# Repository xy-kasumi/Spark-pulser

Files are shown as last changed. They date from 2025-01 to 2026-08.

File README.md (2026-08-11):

# Pulser Board

🚧 Under Construction 🚧

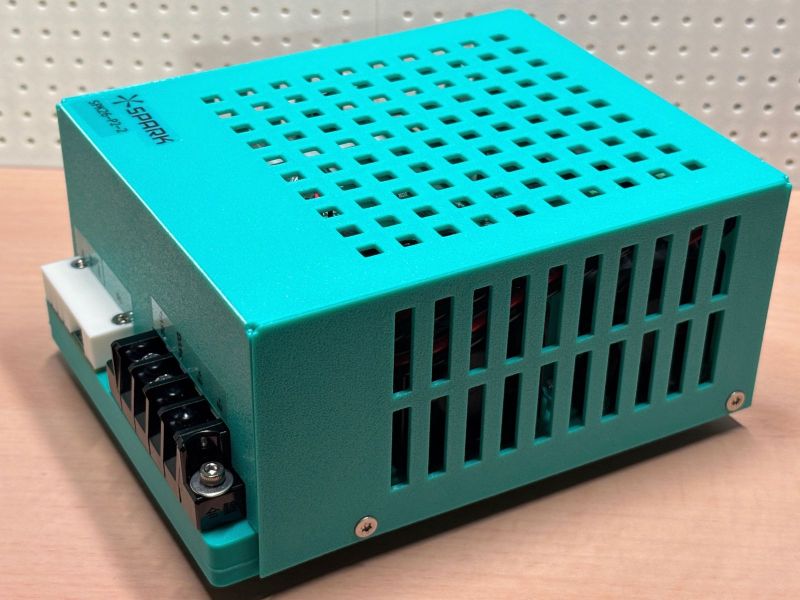
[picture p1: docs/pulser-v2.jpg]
Pulser V2


Open-source EDM module.

Explicitly designed for plunge EDM.
But probably will work for wire EDM too.

Created for https://github.com/xy-kasumi/Spark project.

## Capability (V2)

* 10A max pulse (see [module spec](./docs/pulser.md) for details)
* Designed for reliablity and modular testability (especially stress testing)

Assembly
* PCB (`pcb/` JLCPCB friendly KiCad files (all manufacturable using "Economical PCBA" process))
  * ctrl-r2
  * hv-r4
  * hc-r3
* firmware (ATtiny1616), for `ctrl` and `hv`
* enclosure: 3D print data in `assy`
* needs a few other parts (12V fans & heatsinks)

# Legacy

There was V1 (repo `PULSER-*` tags).
It was "feature-complete", but lacked reliability & testability.

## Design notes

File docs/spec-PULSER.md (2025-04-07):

# PULSER r2 PCB Spec / Cheatsheet for Firmware Developer

This document specifies the PCB hardware interface needed for firmware development,
to meet the requirements defined in [user-PULSER.md](user-PULSER.md).

## Conditions to consider

* Host is not working
  * Control connector is disconnected
  * Host turned off, blank firmware, initializing
* Thermistor wire is broken

Firmware must map these state to well-defined safe behavior.

## uC Overview

uC is Raspberry Pi Pico 2 board.
* [Pico 2 board datasheet](https://datasheets.raspberrypi.com/pico/pico-2-datasheet.pdf)
* [RP2350 chip datasheet](https://datasheets.raspberrypi.com/rp2350/rp2350-datasheet.pdf)

uC operating environment
* 5V 1A powered, regulated down from 12V power
* System clock: 150 MHz
* Firmware write via 3-pin QI connector SWD interface

## uC Connections

| Pin  | Pin Feature  | Connected to | Note |
|---|---|---|---|
| GP0  | I2C0 SDA | I2C_SDA | to host; pulled up to 3.3V by 10kΩ on PCB |
| GP1  | I2C0 SCL | I2C_SCL | to host; pulled up to 3.3V by 10kΩ on PCB |
| GP2  | GPIO (IN) | GATE | to host; direct |
| GP3  | - | - | - |
| GP4  | GPIO (OUT) | LED_STATUS | white LED, digital H = ON |
| GP5  | - | - | - |
| GP6  | - | - | - |
| GP7  | GPIO (OUT) | MUX_V0 | Controls bridge driver V0 (IN) |
| GP8  | - | - | - |
| GP9  | GPIO (OUT) | MUX_VC | Controls bridge driver Vcom (IN) |
| GP10 | - | - | - |
| GP11 | - | - | - |
| GP12 | - | N/C | - |
| GP13 | - | N/C | - |
| GP14 | I2C1 SDA | TS_I2C_SDA | Temp sensor chip I2C |
| GP15 | I2C1 SCL | TS_I2C_SCL | Temp sensor chip I2C |
| GP16 | - | N/C | - |
| GP17 | GPIO (OUT) | GATE_IG | Controls bridge driver for ignition voltage. |
| GP18 | PWM1A (OUT)  | GATE_MAIN_PWM  | Controls buck converter gate |
| GP19 | - | N/C | - |
| GP20 | - | N/C | - |
| GP21 | - | N/C | - |
| GP22 | - | N/C | - |
| GP26 | ADC0 | CURR_DETECT | Current sense chip |
| GP27 | - | N/C | - |
| GP28 | - | N/C | - |

* N/C: No Connection

### Gate input filter
Since correctness of GATE is critical and it's used in noisy environment,
it should employ noise-filtering. (i.e. only detect change if the value persists for more than 1us).

### Pulse generation (GATE_IG, GATE_MAIN_PWM, CURR_DETECT)

Normal operation sequence:
* 0. setup mux
* 1. enable GATE_IG, wait for ignition by monitoring CURR_DETECT
* 2. in parallel:
 * 2.a shutdown GATE_IG after some fixed time (e.g. 10us)
 * 2.b start buck converter, control PWM frequency by monitoring CURR_DETECT

If the ignition time is too short, consider it as short-circuit and don't start buck converter.
Slow GATE_IG shutdown doesn't break anything; rather it just increases time to recover 100V voltage.
Fast GATE_IG means less 100V capacity wasted, but risks premature shutdown of discharge.

Buck converter
* PWM frequency: 500kHz (2us)
* Maximum rate of current change: 36V / 10uH (L4) = 3.6A/us
  * 1% duty: +0.18A/cycle

As there is current sensing delay, PWM duty should start small and change speed should be limited.

#### Current detection

CURR_DETECT is analog output of hole current sensor chip.
ADC Vref is connected to 3.0V reference voltage.
CURR_DETECT is capped by diode to not exceed 3.0V.

* ACS724LLCTR-30AU
* [datasheet](https://www.allegromicro.com/-/media/files/datasheets/acs724-datasheet.ashx)
* "30AU": 0~30A, 133mV/A
* Vout(I=0) = Vcc x 0.1 = 0.5V
* Filter fc=180kHz

Should sample at highest possible ADC resolution to improve current control.

ADC should set PS(GPIO23)=1 to reduce Pico 2 on-board voltage supply ripple.

### Output mux (MUX_*)
Output stage consists of 3 half-bridges.
This enables polarity change & choosing output (work vs grind).

MOSFET driver
* UCC27288
* [datasheet](https://www.ti.com/lit/ds/symlink/ucc27288.pdf)

MOSFETs (both are N-ch)
* BSC110N15NS5
* [datasheet](https://www.infineon.com/dgdl/Infineon-BSC110N15NS5-DataSheet-v02_06-EN.pdf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)

* V0 = WORK
* V1 = GRIND
* VC = TOOL

Allowed configuration:

Keep driver active config
| POLARITY | V0 | VC |
|---|----|----|
| TPWN, TPGN | L  | H  |
| OFF, TNWP, TNGP  | H  | L  |
| Trans | Z  | Z  |

* L: only enable L
* H: only enable H
* Z: disable both

Any any moment, configurations other than this is disallowed.

OFF is L instead of Z, to properly boot-strap gate driver capacitors.

As mux doesn't need fast switching, transition period should be long (more than 500ns)
to avoid any possibility of shoot-through.

Keep driver active config
* pros: easier to ensure gate driver bootstrap
* cons: might cause uncessary electrolysis

Turn-off unused config
* pros: minimize electrolysis, slightly reduce safety risk
* cons: probably need periodic activation to keep driver boostrapped

### Temperature sensor

TMP102 chip
* [datasheet](https://www.ti.com/lit/ds/symlink/tmp102.pdf)
* I2C connection
* ADD0: V+ (see eratta)
* device address: 1001001 (0x49)

The chip is mounted close to hottest MOSFETs.
We need to determine upper bound of operating condition, and reject to run discharges if exceeded.

Registers are 16bit.
Reg 0x00: temperature (12bit, left-padded, big endian.)

Top 8 bit is signed 8 bit int, temperature in °C.

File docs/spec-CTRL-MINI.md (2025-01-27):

# CTRL-MINI-ED (r0) PCB Spec / Cheatsheet for Firmware Developer

This document specifies the PCB hardware interface needed for firmware development,
to meet the requirements defined in [user-README-CTRL-MINI.md](user-README-CTRL-MINI.md).

## Conditions to consider

* MD boards are (partially) unavailable
* ED board is unavailable

Firmware must map these states to well-defined safe behaviors.

## uC Overview

The uC is a Raspberry Pi Pico 2 board.
* [Pico 2 board datasheet](https://datasheets.raspberrypi.com/pico/pico-2-datasheet.pdf)
* [RP2350 chip datasheet](https://datasheets.raspberrypi.com/rp2350/rp2350-datasheet.pdf)

uC operating environment
* 5V 1A powered, regulated down from 12V main power
* System clock: 150 MHz
* Firmware write via 3-pin QI connector SWD interface

## uC Connections

| Pin  | Pin Feature | Connected to | Note |
|---|---|---|---|
| GP0  | UART0 TX | MUI-RX | RasPi probe (serial) |
| GP1  | UART0 RX | MUI-TX | RasPi probe (serial) |
| GP2  | SPI0 SCK | MD (all) | |
| GP3  | SPI0 SDI | MD (all) | |
| GP4  | SPI0 SDO | MD (all) | |
| GP5  | - | ED Conn Pin 3 | N/C (r1), MODE (r0) |
| GP6  | I2C1 SDA | ED Conn Pin 4 | I2C SDA (r1), SENSE_GATE (r0) |
| GP7  | I2C1 SCL | ED Conn Pin 6 | I2C SCL (r1), DCHG_TARG_PWM (r0) |
| GP8  | GPIO (OUT) | ED Conn Pin 7 | GATE (r1), DCHG_GATE (r0) |
| GP9  | GPIO (IN) | ED Conn Pin 8 | DETECT (r1), DCHG_DETECT (r0) |
| GP10 | - | N/C | |
| GP11 | - | N/C | |
| GP12 | - | N/C | |
| GP13 | - | N/C | |
| GP14 | - | N/C | |
| GP15 | - | N/C | |
| GP16 | GPIO (OUT) | MD (all) DIR | |
| GP17 | GPIO (OUT) | MD (0) STEP | |
| GP18 | GPIO (OUT) | MD (1) STEP | |
| GP19 | GPIO (OUT) | MD (2) STEP | |
| GP20 | GPIO (OUT) | MD (0) CSN | |
| GP21 | GPIO (OUT) | MD (1) CSN | |
| GP22 | GPIO (OUT) | MD (2) CSN | |
| GP26 | - | ED Conn Pin 5 | N/C (r1), SENSE_CURR (r0) |
| GP27 | - | N/C | |
| GP28 | - | N/C | |

* N/C: No Connection

MD r0, ED r1 is assumed.
ED r0 pin notes are left for historical reference.

## MD boards

The MD board is a 14-pin child board, taking 3.3V logic power and 12V power input.

Each MD board has:
* A single TMC2130 stepper driver motor
* On-PCB configuration jumpers for:
  * Phase current (0.2A vs 0.4A)
  * Power voltage (5V vs 12V)

They're controlled by SPI & "STEP/DIR" interface.
SPI bus connects uC and 3 MD boards.

To address each chip individually, CSN pins are used.
CSNs are GPIO pins, so firmware needs to manually toggle them when doing SPI transactions.

# ED board

Nothing is done in CTRL-MINI. Just a direct connection.
See [user-README-CTRL-MINI-ED.md](user-README-CTRL-MINI-ED.md) for details.

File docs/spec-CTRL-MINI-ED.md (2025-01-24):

# CTRL-MINI-ED PCB Spec / Cheatsheet for Firmware Developer

This document specifies the PCB hardware interface needed for firmware development,
to meet the requirements defined in [user-README-CTRL-MINI-ED.md](user-README-CTRL-MINI-ED.md).

## Conditions to consider

* Host is not working
  * Control connector is disconnected
  * Host turned off, blank firmware, initializing
* Thermistor wire is broken

Firmware must map these state to well-defined safe behavior.

## uC Overview

uC is Raspberry Pi Pico 2 board.
* [Pico 2 board datasheet](https://datasheets.raspberrypi.com/pico/pico-2-datasheet.pdf)
* [RP2350 chip datasheet](https://datasheets.raspberrypi.com/rp2350/rp2350-datasheet.pdf)

uC operating environment
* 5V 1A powered, regulated down from 36V main power
* System clock: 150 MHz
* Firmware write via 3-pin QI connector SWD interface

## uC Connections

|Pin | Pin Feature | Connected to | Note |
|----|---|---|---|
|GP0 | I2C0 SDA | I2C_SDA | to host; pulled up to 3.3V by 10kΩ on PCB |
|GP1 | I2C0 SCL | I2C_SCL | to host; pulled up to 3.3V by 10kΩ on PCB |
|GP2 | GPIO (IN) | GATE | to host; direct |
|GP3 | GPIO (OUT)  | DETECT  | to host; direct |
|GP4 | GPIO (OUT)  | LED_STATUS | white LED, digital H = ON |
|GP5 | GPIO (OUT)  | LED_POWER  | red, digital H = ON |
|GP6 | - | N/C | |
|GP7 | - | N/C | |
|GP8 | GPIO (OUT)  | MUX_POL = POL | Relay gate drive. OFF: COM(TOOL)=-,VO_AUX=+, ON: COM(TOOL)=+, VO_AUX=- |
|GP9 | GPIO (OUT)  | MUX_WG = SEL | Relay gate drive. OFF: V0(WORK)=ON, ON: V1(GRINDER)=ON |
|GP10| GPIO (OUT)  | MUX_EN = EN | Relay gate drive. OFF: cut off driver, ON: connect driver |
|GP11| - | N/C | |
|GP12| - | N/C | |
|GP13| - | N/C | |
|GP14| - | N/C | |
|GP15| - | N/C | |
|GP16| GPIO (IN) | CURR_TRIGGER | 3.3V output from Comparator U5 |
|GP17| - | N/C | |
|GP18| PWM1A (OUT) | CURR_GATE_PWM | analog filter; see below |
|GP19| - | N/C | |
|GP20| PWM2A (OUT) | CURR_THRESH_PWM | analog filter; see below |
|GP21| - | N/C | |
|GP22| - | N/C | |
|GP26| ADC0 | TEMP_HS | Thermistor - resistor voltage divider |
|GP27| - | N/C | |
|GP28| - | N/C | |

* N/C: No Connection

### Pulse generator (CURR_GATE_PWM, CURR_THRESH_PWM, DETECT)
Main MOSFET current flow
```
100V|36V --(E+)-- discharge gap --(E-)-- drain:MOSFET:source --(FB)-- 220mΩ(±5%) --- GND
```

Voltage at FB is used for current feedback control of MOSFET driving, and also for current detection.

| ΔIp or Ip | FB | GATE | Approx |
|---|----|---|---|
| ΔIp = 100mA | ΔFB = 22mV (min: 21mV, max: 23mV) | ΔGATE = 37mV | 1/89 x 3.3V |
| Ip = 1A | FB = 0.22V (min: 0.21V, max: 0.23V) | GATE = 0.37V | 10/89 x 3.3V |
| Ip = 8A | FB = 1.76V (min: 1.67V, max: 1.85V) | GATE = 2.98V | 80/89 x 3.3V |

#### Current / voltage control
```
CURR_GATE_PWM --> gate-filter --(CURR_GATE)--> feedback-controlled MOSFET
CURR_THRESH_PWM --> thresh-filter --> -:voltage comparator
CURR_DETECT <-- voltage comparator:+ <-- FB filter --- FB
```

#### Gate filter
```
CURR_GATE_PWM (3.3V digital) --> 59% volt divider (Z=278Ω) --> 10uH --(pull down via 10nF) --> +:controller opAmp
```

This forms 2nd-order LPF with Fc=500kHz.
Simulation shows that
* 1us rise time for step input
* 2MHz PWM yields ripple of up to 5% of full scale (0.17V; corresponds to 750mA in Ip)
  * 2MHz PWM means 75 cycles (sys clock = 150MHz)
* allows room for current-shaping in the future

To achieve more accurate current control, pre-computed delta-sigma pattern table and PIO should be used.

#### Thresh filter
```
CURR_THRESH_PWM (3.3V digital) --> 10kΩ --(pull down via 10nF) --> -:voltage comparator
```
1st order LPF with Fc=1.6kHz.
1MHz PWM should yield accurate enough analog signal.

#### FB filter
FB signal goes through 2nd order LPF with Fc=1MHz to suppress noise.
This might introduce latency of 1us, but there's nothing uC can do.

### Relays (MUX_EN, MUX_POL, MUX_WG)
```
uC pin --- 1kΩ --(pull down via 47kΩ)-- gate:MOSFET
+12V --- relay coil (+ flywheel diode) -- drain:MOSFET:source --- GND
```

MOSFET gate has ringing-limiting in-line resistor (1k), and pull-down (47k).

Thus, when uC is not iniailized (high-Z GPIO), relay is OFF. uC also doesn't need to pull-down.

MOSFET: Vishay Si2304DDS
* [datasheet](https://www.lcsc.com/datasheet/lcsc_datasheet_2410121816_Vishay-Intertech-SI2304DDS-T1-GE3_C56372.pdf)
* Full-turn on around Vgs~3V

Relay: Omron G2RL-24 DC12
* [datasheet](https://omronfs.omron.com/en_US/ecb/products/pdf/en-g2rl.pdf)
* 2-pole (DPDT; 2c), sealed, 12V coil
* coil current 33mA, 12V
* turn on time: 15ms max
* turn off time: 5ms max
* rated switching load: 8A @ 30VDC (durability: 30K operations)
* rated carry current: 8A @ 70℃
* contact resistance: 100mΩ max

### Temperature sensor (TEMP_HS)
connection: 3.3V --- thermistor --(TEMP_HS)-- 47k --- GND

thermistor: 100kΩ NTC thermistor
* EPCOSB57861S0104F040
* R(T=25℃): 100kΩ±1%
* B-value: 4540K±1%
* [datasheet](https://docs.rs-online.com/838f/0900766b815ec91a.pdf)

This graph/table shows relationship within 5℃ accuracy.

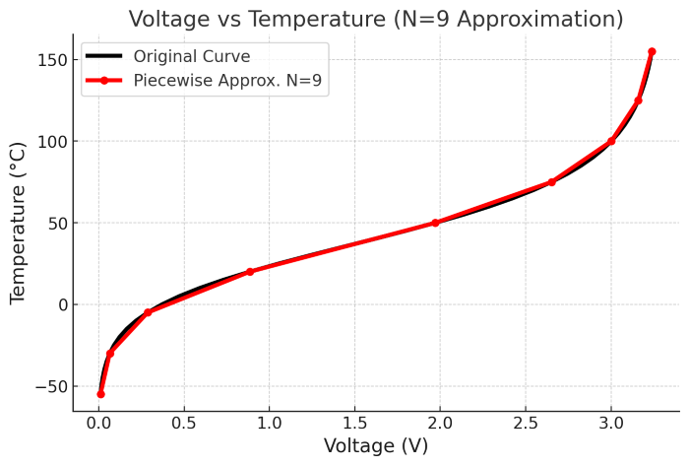
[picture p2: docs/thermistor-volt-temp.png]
thermistor-temp


TEMP_HS(V) | Temp(°C)
-----|-----
0.29 | -5
0.89 | 20
1.97 | 50
2.65 | 75
3.01 | 100
3.16 | 125

Outside this range, firmware should refuse to run (show error) until reset.

Thermistor is inserted to heatsink with silicon heat paste.

Heasink has MOSFET (Q4), resistor (R17), OR-diode (D6).
They're pretty heat resistant. However, it's better to think 60℃ or close as max allowed temp for heatsink.

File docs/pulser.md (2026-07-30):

# Pulser V2

Features
* Iso-pulse control
* Max 10A pulse current
* Isolated I2C control & feedback interface

See [operation model](./operation.md) for how output works.

## Interface

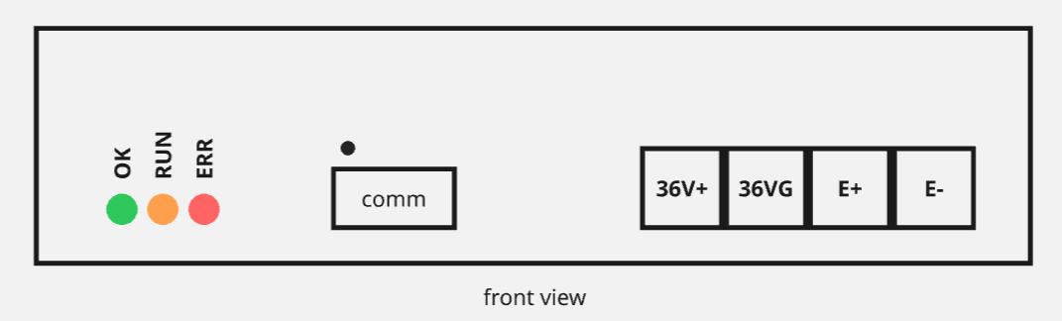
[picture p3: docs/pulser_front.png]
Front View


### Indicators

* OK (green): indicates succesful boot up of the module
* RUN (amber): indicates output is enabled
  * Warning: OFF does NOT means output is safe to touch (might still be charged due to residual capacity)
* ERR (red): indicates fault

### Comm

XH 3 pin, I2C Fast Mode Plus (5V logic)
* 1:SDA 2:SCL 3:GND

Comm pins are isolated from power terminals.

See [I2C Register Map](./i2c-registers.md) for control.

### Power

Terminal Block
* 36V+, 36VG, E+, E-

note: E- and 36VG are internally connected.

## Mounting

* Dimensions: TBD
* Weight: TBD

Can mount to DIN rail.

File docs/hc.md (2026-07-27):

# Pulser HC (High-Current) Board / Module

## Interfaces

### Mechanical

Terminals
* I+/I-: 36V DC, max draw 10A
* O+/O-: pulse output

FFC P=1mm
* 1:VCC 2:GND 3:EN 4:CURR 5:GND 6,7,8:NC

### Electric
Isolated digital
* VCC: 5V or 3.3V (digital I/O voltage), <5mA
* EN: input
* CURR: input (PWM, 10kHz~200kHz)

CURR specifies output current.
* Setting delay: 10ms
* Working range: 22%(5A) - 45%(10A) (0.22A/pt)
  * Below 22%: tries to output specified current, but ripple dominates
  * Above 45%: internally clamped to 10A

Indicators
* PWR (green): board is powered
* EN (amber): EN is active

## Characteristics

### T_rise
Time between: EN rise (in input) & output current crossing 1A.

Measurement condition:
* 20V diode load
* EN L->H

Reference data
* CURR=5A, T_rise=11.7us
* CURR=10A, T_rise=8.8us

### T_fall
Time between: EN fall (in input) & output current crossing 0.5A.

Reference data
* CURR=5A, T_fall=33us
* CURR=10A, T_fall=42us

## Stress Tests

### Heat Dissipation
Measurement condition
* Fan & duct assembled
* EN=H (continuous)
* CURR=10A
* 20V diode load, short load

Visible surface temerature must not exceed 110 ℃

With (10mm)^3 heatsink attached on top of D1,
D1 (max temp) is measured as 105℃.

### Voltage Overshoot
Measurement condition
* CURR=10A
* EN=H (continuous)
* repeated open<->short, load<->open, load<->short
  * Use external MOSFET-switch to simulate load disconnect

* Output voltage must not exceed 115V at any point (threshold trigger for more than 30sec)
* Internal MOSFET (Q1, Q2) Vds & Vgs must not exceed 90% of abs. max

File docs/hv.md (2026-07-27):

# Pulser HV (High-Voltage) Board / Module

Features

* 1A (approx), 95V output
* Max 10us pulse

## Interfaces

### Mechanical
Terminals
* I+/I-: 36V DC, max draw 2A
* O+/O-: pulse output

FFC P=1mm
* 1:VCC 2:GND 3:EN 4:CURR 5:GND 6:!FAULT 7,8:NC

### Electric
I-/O- shares power ground. All pins in FFC connector is isolated from I/O power rails.

Isolated digital
* VCC: 5V or 3.3V (digital I/O voltage), <5mA
* EN: input
* CURR: output
* !FAULT: output

Indicators
* PWR/STAT (green): uC is running
* CURR (amber): output current is detected
* ERR/FLT (red): uC has detected hardware/firmware fault (latches until power cycle)

When EN is H, voltage is applied to output.
CURR indicates current is flowing through output.

Output is disabled, and kept disabled when
* 10us passed since CURR rise
* EN is lowered

To start next cycle, EN must be lowered and risen again.

For thermal protection, HV board limits duty to 10%.
When CURR rises, internal cooldown counting of 100us starts.
EN rise is ignored until 100us passes.
Host is recommended to wait 110us or more before raising EN again after CURR detection.

## Characteristics

### T_detect
Time between output current & CURR rise (crossses 200mA).

Measurement condition
* 20V diode load
* Measure EN rise - CURR rise (provides upper bound, b/c current output rise time is also included)

Reference data
* < 0.5us

### T_delay
Time between EN rise & CURR rise.

Measurement condition
* 20V diode load

Reference data
* 2us

## Stress Test

### Heat Dissipation
Measurement condition
* fan & duct assembled
* short load
* EN: max density pulse (on:10us, off:100us)

Visible surface temperature must not exceed 100℃

Measured: 82℃

### Voltage Overshoot
Measurement condition
* CURR=10A
* EN: pulse (10us)
* repeated open<->short, load<->open, load<->short
  * Use external MOSFET-switch to simulate load disconnect

* Output voltage must not exceed 115V at any point (threshold trigger for more than 30sec)
* Internal MOSFET (Q1, Q2) Vds & Vgs must not exceed 90% of abs. max

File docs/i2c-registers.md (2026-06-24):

# Register Map

* 7-bit I2C device address: 0x3c

| Address | Register | Access |
|---|---|---|
| 0x01 | CTRL | RW |
| 0x02 | MODE | RW |
| 0x03 | CURR | RW |
| 0x04 | DUR | RW |
| 0x05 | DUTY | RW |
| 0x08 | RES0 | R |
| 0x09 | RES1 | R |
| 0x10 | FAULT | R + clear  |

Supported operational range
* current: 10A
  * duration: 100us~950us / duty: 1%~49%
  * duration: 25us~95us / duty: 1%~19%
* current: 1A
  * duration: 10us / duty: 1%~9%

Auto-clamping works like:
* CURR: calmps on its own
* DUR: clamps based on current CURR
* DUTY: clamps based on current CURR & DUR

## CTRL
Controls device run status.

`| reserved: 7 | run: 1 |`

* default: 0x00

`run := 1` activates output.
Read of `run` indicates whether device is running or not.

Device stops running when:
* `run := 0`
* `probe` mode finishes
* fault happens

When device is running, watch dog timer (WDT) of 50ms is active.
Reading `RES0` is the only way to reset WDT.
WDT timeout is considered a fault.

## MODE
**default: 0x00**

Run mode. Write fails when device is running.

`| reserved: 7 | mode: 1 |`

mode
* 0: `probe` mode
* 1: `cut` mode

### `probe` mode
Uses electrodes to detect conduction with minimum current & duration.
It does not use CURR or TIM settings.
Once it detects conduction, device stops after setting `RESULT` register.

### `cut` mode
Iso-pulse continuous run mode. Uses `CURR`, `TIM` register values.

## CURR
**default: 0x0a**

Pulse current configuration. Write fails when device is running.

`| curr: 8 |`

`curr` specifies pulse current in Amperes.
Written value is clamped to closest device-supported value.

## DUR
**default: 0x42** (100us)

`| reserved: 1 | exp: 2 | frac: 5 |`

Allowed `frac` is 0..19 (20..31 are reserved).

* exp==0: 10us
* exp==1: 100us
* exp==2: 1000us
* exp==3: reserved

`pulse duration = multiplier * (frac / 20)`

e.g. 0x01 (exp==0, frac==1): 10us x (1 / 20) = 0.5us (min positive value)
e.g. 0x42 (exp==2, frac==2): 1000us x (2 / 20) = 100us
e.g. 0x53 (exp==2, frac==19): 1000us x (19 / 20) = 950us (max value)

## DUTY
**default: 0x7c** (49%)

Limits the max duty by varying minimum cooldown time between pulses, as `(DUTY + 1) / 256`.

## RES0..1
**default: 0x00,0x00**

Pulse result and WDT clearing.

Reading `RES0` causes WDT clearing and result value update.
Result registers shows statistics between previous read (or run start).

Host can retrieve (RES0, RES1) atomically by normal sequential read of `RES0->RES1`.

### `cut` mode
* `RES0`: `| fault: 1 | reserved: 1 | r_open: 3 | r_short: 3 |`
* `RES1`: `| num_good: 8 |`

* ratio (num_open / num_window): `r_open / 7`
* ratio (num_short / num_window): `r_short / 7`
* number of good pulse: `num_good`

The count does not include ongoing open window.

`r_open` & `r_short` can be used for EDM feedback control (open: advance, short: retract).
If there's no data to compute ratios (immediate read after start), `r_open==7` & `r_short==0` will be returned.

`num_good`, in conjunction with pulse duration, can be used to compute "effective duty",
which is a good proxy for MRR (material removal rate) and power dissipation.
* `effective duty` = `duration of good pulse / entire duration` = `pulse_dur * num_good / time_between_read`

`num_good` count saturates at 255. Host must poll fast enough to get accurate value w/o saturation.

note: since `r_{open,short}` represents ratios, `r_open + r_short <= 7` holds.

### `probe` mode
Only `RES0` is used.

* `RES0`: `| fault: 1 | reserved: 6 | detected: 1 |`
* `RES1`: `| reserved: 8 |`

Unlike in `cut` mode, reading will not clear the result.

## FAULT
**default: 0x00**

`| reserved: 6 | wdt: 1 | fault: 1 |`

`wdt==1` indicates WDT timeout has happened. Writing 1 clears this bit.
`fault==1` indicates device has some kind of fault, and cannot run. Writing 1 is no-op.

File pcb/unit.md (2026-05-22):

# Test unit wiring
Unit consists of 3 boards (CTRL, HV, HC; all under `pcb/`) & terminal unit.

## TU (Terminal Unit)

### Inner interface
E+, E-, P+, PG, I-SDA, I-SCL, I-GND

### Outer interface
(from left to right)

TBOUT (screw terminal block)
1. E+
2. E-

TBIN (screw terminal block)
1. +36V (P+)
2. GND (PG)

I2C (XH 3 pin socket)
1. SDA (I-SDA)
2. SCL (I-SCL)
3. GND (I-GND)

## Wiring

* TU.E+: HV.E+, HC.E+
* TU.E-: HV.E-, HC.E-
* TU.P+: HV.36V+, HC.36V+, CTRL.36V
* TU.PG: HV.36VG, HC.36VG, CTRL.GND
* (I-SDA, I-SCL, I-GND): CTRL.(SDA, SCL, GND)

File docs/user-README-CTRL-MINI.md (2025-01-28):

# CTRL-MINI (r0) User Manual

This doc is for users of the CTRL-MINI board.
It serves as both a datasheet and an operating manual.

## Overview

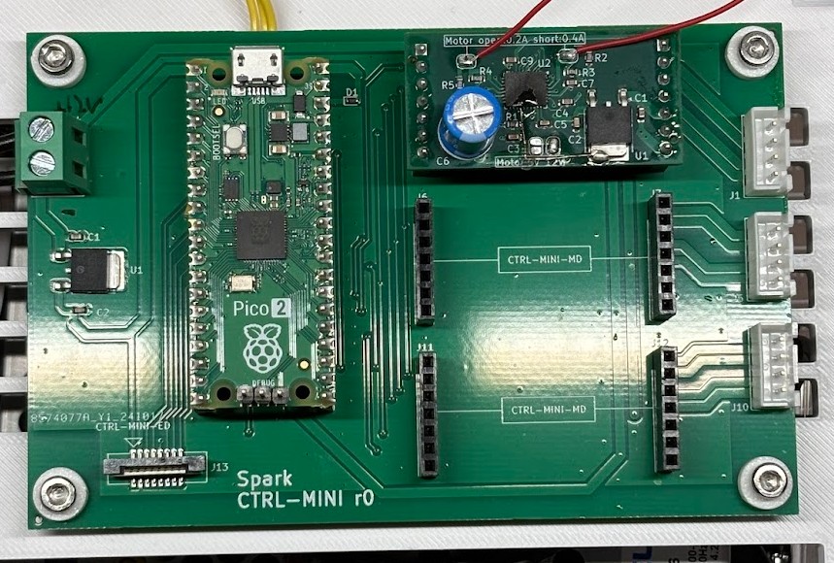
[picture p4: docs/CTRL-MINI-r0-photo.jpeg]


CTRL-MINI is the main board of a Spark machine.
In the current prototype phase, it serves as an experimental hub.
Major revisions are expected in future iterations.

It features the following functionality:
- Terminal-like interface for human operator via RasPi probe
- 3-axis bipolar stepper motor driver with swappable child boards (CTRL-MINI-MD)
  - 12V, 0.4-ish A per phase
  - Features Trinamic TMC2130 driver with 1/256 microstepping capability
- Connectivity to CTRL-MINI-ED board

Note: The architectural relationship between CTRL-MINI and CTRL-MINI-ED (whether as a sub-component or separate board) is TBD. This document treats it as a separate board.

### Power Supply

Screw terminal on the left side:
- Input: 12VDC
- Current: 2A minimum recommended
  - 1A minimum if using reduced motor current
  - Higher current ratings are OK

### Connections

Right edge: Motors
- 3x XH connectors
  - Pin configuration (top to bottom):
    1: A1
    2: A2
    3: B1
    4: B2

Bottom edge: CTRL-MINI-ED connection
- Upright connector for FFC (Flat Flexible Cable)
  - Type-A, pitch 1mm, 8 pins
  - Terminal thickness: 0.3mm

Top edge: RasPi Probe (Serial Communication)
- QI female 3-pin connector
  1: TX
  2: RX
  3: GND

### Mechanical
Reference orientation: "Spark" text on board facing up

**General**
* Outer dimensions: 115mm (width) x 75mm (height) x 25mm (depth)
* Mass: to-be-measured

**Mounting**
Board dimensions: 115mm (width) x 75mm (height)
- 4x mounting holes:
  - Coordinates: (5mm, 5mm), (5mm, 70mm), (110mm, 5mm), (110mm, 70mm)
  - Hole diameter: 3.3mm
  - Clearance for screw head/spacer: 8mm diameter
  - Mounting areas are electrically isolated

## Terminal Interface

Connect the RasPi probe's serial port to the 3-pin QI connector.
Use any terminal emulator software on the host computer.

Required configuration:
- Baud rate: 115200

Recommended configuration:
- Line ending: CR (for both TX/RX)
- Local echo: ON

Interface behavior:
- Commands are single-line only (no multi-line support)
- Input control:
  - `Ctrl-C` or `Ctrl-K`: Cancel current command
  - Other control keys are not supported (backspace, arrows, delete)

### High-Level Commands

#### `status`
* **Description:** Prints the status of the system.

#### `edparam <duration_us> <duty> <current_ma>`
* **Description:** Configures pulse duration, duty factor, current. Will affect `drill` command.
* **Parameters:**
  * `duration_us`: integer, pulse duration in microseconds (range: 5 to 10000)
  * `duty`: integer, max duty ratio in percent (range: 1 to 50)
  * `current_ma`: integer, current in mA (range: 100 to 8000). Will be rounded down to possible value.

#### `move <board_ix> <distance>`
* **Description:** Moves the specified board by a given distance (in millimeters).
* **Parameters:**
  * `board_ix`: 0, 1, or 2
  * `distance`: float (in mm)

#### `find <board_ix> <distance>`
* **Description:** Moves up to a specified distance or until the electrode touches the work.  
  Uses a hot electrode scan and may cause slight damage to the work.
* **Important:** Must be issued after `edon`.
* **Parameters:**
  * `board_ix`: 0, 1, or 2
  * `distance`: float (in mm)

#### `drill <board_ix> <distance>`
* **Description:** Drills by a specified distance. Actual drill depth may be less due to tool wear.
* **Important:** Must be issued after `edon`.
* **Parameters:**
  * `board_ix`: 0, 1, or 2
  * `distance`: float (in mm)

### Motor Driver (MD) Commands

#### `step <board_ix> <step> <wait>`
* **Description:** Steps one motor in one direction at a constant speed.
* **Parameters:**
  * `board_ix`: 0, 1, or 2
  * `step`: integer (negative or positive), in microsteps
  * `wait`: integer, wait time after each microstep, in microseconds

#### `home <board_ix> <direction> <timeout_ms>`
* **Description:** Moves the motor to the home position (where it stalls).
* **Parameters:**
  * `board_ix`: 0, 1, or 2
  * `direction`: `-` or `+`
  * `timeout_ms`: integer, timeout in milliseconds

#### `regread <board_id> <addr>`
* **Description:** Reads a register from peripheral boards.
* **Parameters:**
  * `board_id`: 0, 1, 2, E
  * `addr`: hexadecimal value from `00` to `7f`

### Low-Level Commands

#### `regwrite <board_id> <addr> <data>`
* **Description:** Writes to a register on the peripheral boards.
* **Parameters:**
  * `board_id`: 0, 1, 2, E
  * `addr`: hexadecimal value from `00` to `7f`
  * `data`: hexadecimal, 1-byte for E, 4-byte for 0,1,2
* **Examples:**
  * `regwrite E 02 01`
  * `regwrite 0 10 1f10`

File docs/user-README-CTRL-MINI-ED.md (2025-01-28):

# CTRL-MINI-ED (r1) User Manual

This doc is for users of the CTRL-MINI-ED board.
It basically serves as both a datasheet and an operating manual.

## ⚠️ Safety warning ⚠️
Improper use of CTRL-MINI-ED may cause death, fire, or damage to nearby devices.

## Overview

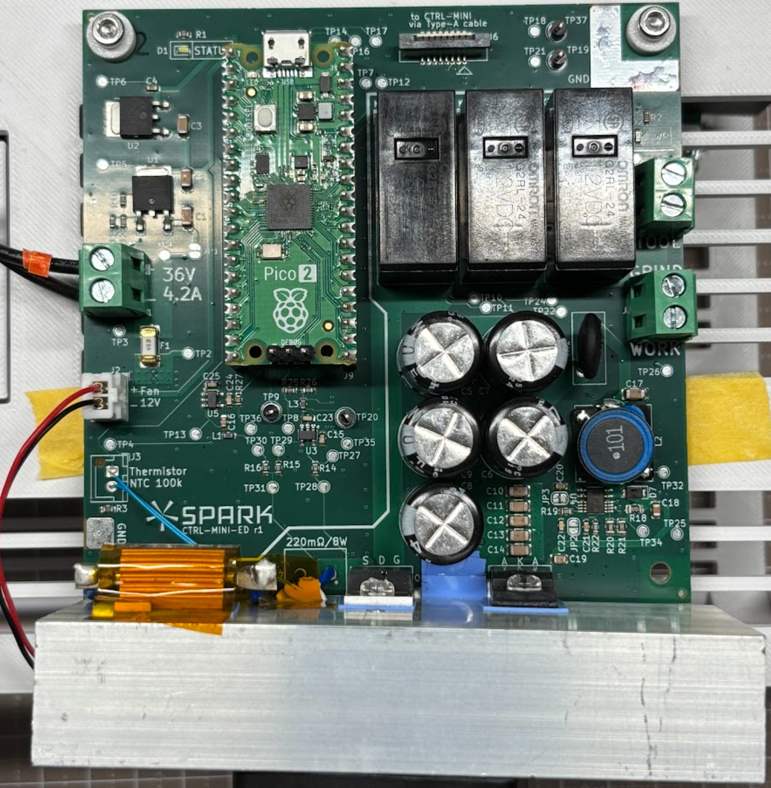
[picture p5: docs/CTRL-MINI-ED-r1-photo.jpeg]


CTRL-MINI-ED is an EDM discharge board, controllable via digital IOs and I2C.

* Max pulse current: 8A (at duty factor=50%)
* Open voltage: 100V
* 5 dynamic polarity configurations
  * (Tool+, Work-), (Tool-, Work+)
  * (Tool+, Grinder-), (Tool-, Grinder+)
  * Disconnected
* Single-pulse discharge timing control, and pulse current detection via GATE/DETECT digital IOs
* Pulse current, detection threshold, polarity control, temperature monitoring via I2C

### Power Supply
Screw terminal on the left side
* DC 36V, 4.2A minimum

If the power supply is below 4.2 A, the microcontroller might reset accidentally at high-power setting.
Above 4.2 A should be fine, but too much output (e.g. 10 A) will increase the damage in case of firmware bug.

### Indicators

* Status (white) LED: ON if OK. Blinks if error. OFF means hardware or firmware failure.
* Power (red) LED: Indicates that electrodes are potentially energized. Blinks if error.

Even after sudden power failure, electrodes should be in high-impedance state if the Power (red) LED is OFF.
When the board enters an error state, the only way to recover is through a power reset.

### Connections

Control Connector:
* Upright connector for FFC (Flat Flexible Cable)
  * Type-A, pitch 1mm, 8 pins, terminal thickness 0.3mm

Electrodes:
* three screw-terminals on the right side ("Wire", "Grind", "Tool" marking on the PCB)

### Mechanical & Thermal
* Listed values are board with heatsink and fan
* "height", "width" etc. is based on "Spark" logo on the board

**General**
* Outer dimensions: 135mm (width) x 105mm (height) x 50mm (depth)
* Mass: 240g

**Mounting**
Board dimensions: 100mm (width) x 100mm (height)
* 4 mounting holes at (5mm, 5mm), (5mm, 95mm), (95mm, 5mm), (95mm, 95mm)
* Hole dia: 3.3mm, dia available for screw head, spacer etc: 6.5mm
  * available area is either isolated or GND

**Thermal**
* Max heat generation: 75W
  * Ensure adequate airflow at the bottom of the PCB for proper fan operation.

## Controller Interface

CTRL-MINI-ED is designed to be safe (de-energized) to be turned on with "Control Connector" disconnected.

### Physical layer
"Control Connector" pinout (at **host-side**. See note.):
1. Don't Connect
2. GND
3. Don't Connect
4. I2C SDA
5. Don't Connect
6. I2C SCL
7. GATE
8. DETECT

Note: Type-A (terminals on same-side) means cross-cable. Thus, pinout at host and ED board is flipped.

* I2C SDA/SCL: 3.3V I/O. Standard Mode (~100kHz). Pulled-up in ED board.
* GATE: 3.3V digital input
* DETECT: 3.3V digital output

### I2C layer

* Device Address: 0x3B
* Speed: Standard Mode (~100kHz clock)

Within the device, there are registers with 1-byte address and 1-byte data.
Write command writes to a single register, Read command read from a single register.

They involve internal pointer. They don't auto-increment.

**Write**
* M: START
* M: Device Addr (7bit; 0x3B) + Write flag (1bit; 0)
* S: ACK
* M: Register Addr (8bit)
* S: ACK
* M: Data (8bit)
* S: ACK
* M: STOP

This also sets the internal pointer to Register Addr.

**Read**
(write pointer)
* M: START
* M: Device Addr (7bit; 0x3B) + Write flag (1bit; 1)
* S: ACK
* M: Register Addr (8bit)
* S: ACK
(read data from pointer)
* M: Repeated START
* M: Device Addr (7bit; 0x3B) + Read flag (1bit; 1)
* S: Data (8bit)
* M: NACK
* M: STOP

(M: master, S: slave)

### Logical layer

### GATE/DETECT
The host can initiate a single pulse by setting GATE to HIGH.
If the discharge condition is good, discharge will happen after a random Tig (ignition time).
Tig is inherently random, but typically ranges from 10μs to 500μs, and becomes shorter if the gap is narrower.

If DETECT becomes HIGH very quickly (within 5μs), it is highly likely that the discharge gap is short-circuited.
In that case, the host should set GATE to LOW immediately.

Generally, GATE can be thought of as directly driving the MOSFET gate. However, for safety and device longevity,
actual driving can be suppressed. See the "Timing wrt. GATE/DETECT" section for details.

DETECT becomes HIGH whenever discharge current is detected.
The host is responsible for monitoring DETECT and setting GATE to LOW after the desired pulse duration time.
The current detection threshold is auto-set to 25% of pulse current by the ED board.

When POLARITY or PULSE_CURRENT is updated, DETECT can become LOW even when actual discharge
current is still flowing.



There is a constraint for combinations of pulse time, pulse current, and duty factor.
See the "Pulse Shaping" section for details.

Safety note: electrodes are **energized even when GATE is LOW**

Setting GATE to LOW merely means turning down the current close to 0.
However, open voltage of 100V is still present on the electrodes,
and the driver will allow more than 10mA current to flow, which is enough to kill you.

To actually turn them off, you need to set POLARITY to OFF.

### Control Registers
|Address| Register | Access | Resets to | Description |
|---|---|---|---|---|
| 0x01  | POLARITY | RW | 0 | 0: OFF, 1~4: energize with certain polarity. |
| 0x02  | PULSE_CURRENT | RW | 10 | pulse current in 100mA step. 1 (100mA) ~ 80 (8A) is allowed. |
| 0x03  | TEMPERATURE | R | N/A | current heatsink temperature in ℃. 80 means 80℃. 255 means temp reading is unavailable due to severe issue. |

Register access:
* RW: read-write
* R: read-only

Invalid value writes are:
* set to safe default such as OFF (e.g. POLARITY)
* set to nearest valid value (e.g. PULSE_CURRENT)
* ignored for read-only or unused registers (e.g. TEMPERATURE)

#### Timing wrt. GATE/DETECT

Writes to POLARITY & PULSE_CURRENT immediately updates the register.
However, when register is changed during GATE is HIGH,
* change will take effect from the next pulse (once GATE become LOW)
* actual EDM driver will be suppressed for 1ms (PULSE_CURRENT change) and 20ms (POLARITY change)
  * this will lead to very large observed DETECT from the host

As an exception to the delay above, setting POLARITY to OFF immediately shutdown EDM driver.

#### POLARITY

* 0: OFF
* 1: TPWN (Tool+, Work-)
* 2: TNWP (Tool-, Work+)
* 3: TPGN (Tool+, Grinder-)
* 4: TNGP (Tool-, Grinder+)

### Pulse Shaping

Pulse current is limited due to the internal capacitor bank.
* Always: Ip <= 8A (enforced by register)
* When Ip >= 4A: Tp <= 8mC / Ip
  * Tp (max) = 1ms @ Ip = 8A
  * Tp (max) = 1.3ms @ Ip = 6A
* When Ip >= 4A: Ip * DF <= 4A
  * DF (max) = 50% @ Ip = 8A

If DF or pulse duration exceeds these values, discharge current will dwindle to 4A (power supply current) or cause an abrupt voltage drop.

The ED board driver is optimized for EDM. It uses a combination of:
* 100V low-capacity "ignition supply"
* 36V high-capacity "discharge supply"

This is possible because the gap voltage, once ignited, becomes about 20V (up to ~30V, depending on conditions).
This dual supply driver is power-efficient but produces unexpected behavior when connected to non-discharging loads.

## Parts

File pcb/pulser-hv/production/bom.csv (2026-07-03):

Designator | Footprint | Quantity | Value | LCSC Part #
C1, C10, C3 | 1206 | 3 | 100nF 200V | C113894
C11, C29, C30, C8 | 0603 | 4 | 1u | C15849
C12 | 0603 | 1 | 0.22u | C21120
C13 | 0603 | 1 | 1n | C1588
C14, C15, C16, C17 | 0603 | 4 | 0.1u
C2 | 1812 | 1 | 1uF 200V | C3037685
C21, C4, C5, C6, C7 | 0603 | 5 | 0.1u | C14663
C26 | 0402 | 1 | 1u | C52923
C27 | 0603 | 1 | 10u | C96446
C9 | 1206 | 1 | 10uF 50V | C13585
D1, D2, D5 | D_SMC | 3 | 150V 2A | C241922
D3 | 0603 | 1 | LED | C165983
D4 | 0603 | 1 | LED | C126319
D6 | D_TUMD2 | 1 | 150V 250mA | C509964
D7 | 0603 | 1 | LED | C2286
F1 | Fuse_Littelfuse-NANO2-451_453 | 1 | 2A | C142852
J1, J2 | Wurth_TerminalBlock_2pin_P5mm_691137710002 | 2 | Screw_Terminal 2pin | C8269
J3 | JST_XH_B2B-XH-A_1x02_P2.50mm_Vertical | 1 | Conn_01x02_Pin | C158012
J5 | PinSocket_1x02_P2.54mm_Vertical | 1 | Conn_01x02_Socket | C7499322
J6 | Molex_200528-0080_1x08-1MP_P1.00mm_Horizontal | 1 | Conn_01x08_Pin | C6074066
L1 | L_12x12mm_H8mm | 1 | 150uH | C338769
Q1 | SOT-223-3_TabPin2 | 1 | Q_NMOS_GDS | C537930
R1 | 1206 | 1 | 100mΩ 120V | C25334
R10 | 0402 | 1 | 10k | C513708
R14 | 0603 | 1 | 270 | C22966
R15 | 0603 | 1 | 820 | C23253
R16 | 1206 | 1 | 430k
R17, R19, R20, R21 | 0603 | 4 | 100k | C25803
R18 | 0603 | 1 | 7.5k | C23234
R2, R7 | 0603 | 2 | 4.7k | C23162
R3 | 1206 | 1 | 100k | C17900
R4 | RESI-TO263 | 1 | 100 | C37794578
R6 | 0603 | 1 | 1k | C21190
R9 | 0402 | 1 | 110k | C138065
U1, U7 | SOIC-8_3.9x4.9mm_P1.27mm | 2 | ADuM1200AR | C15219
U11 | VQFN-20-1EP_3x3mm_P0.4mm_EP1.7x1.7mm | 1 | ATtiny1616-M | C507118
U2 | SOT-23-5 | 1 | INA281A2 | C2908677
U3 | MSOP-10-1EP_3x3mm_P0.5mm_EP1.68x1.88mm | 1 | LTC7001 | C690094
U4 | SOT-23-5 | 1 | TLV3201 | C105188
U5 | TO-252-2 | 1 | LM317_DPAK | C68136
U6 | AD-MSOP-LT8365 | 1 | LT8365 | C673785
U9 | TI-RDN0011A-MFG | 1 | TPSM365R6 | C6723000

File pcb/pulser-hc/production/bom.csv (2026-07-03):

Designator | Footprint | Quantity | Value | LCSC Part #
C1, C4 | 0402 | 2 | 1n | C1523
C10, C11, C21, C23, C24, C25 | 1206 | 6 | 10u | C13585
C12 | 0805 | 1 | 22n | C5128361
C14 | 0603 | 1 | 2.2u | C23630
C15, C16, C33, C35 | 0402 | 4 | 0.1u | C307331
C17, C18 | 0402 | 2 | 10n | C15195
C19, C20, C5 | 0805 | 3 | 10u | C1713
C2, C8 | 0603 | 2 | 220n | C21120
C22 | 1206 | 1 | 10u | C89632
C26 | 0402 | 1 | 1u | C52923
C27 | 0603 | 1 | 10u | C96446
C29, C30 | 0603 | 2 | 1u | C15849
C3 | 0402 | 1 | 22n | C1532
C6 | 0402 | 1 | 470p | C26412
C7 | 0402 | 1 | 4.7n | C1538
C9 | 0805 | 1 | 1u | C28323
D1 | VISHAY-SMPC | 1 | ~ | C968542
D2 | D_SOD-123 | 1 | ~ | C177047
D3 | D_SOD-123 | 1 | D | C177047
D4 | TO-227A-2P | 1 | Ipeak>10A | C2927414
D5 | D_SMB | 1 | Vz=100V | C150045
D6 | TO-227A-2P | 1 | ~ | C2927414
D7 | 0805 | 1 | LED | C2297
D8 | 0805 | 1 | LED | C5123498
F1 | Fuse_Littelfuse-NANO2-451_453 | 1 | 10A | C44479
J1, J2 | Wurth_TerminalBlock_2pin_P5mm_691137710002 | 2 | Screw_Terminal 2pin | C8269
J3 | JST_XH_B2B-XH-A_1x02_P2.50mm_Vertical | 1 | Conn_01x02_Pin
J6 | Molex_200528-0080_1x08-1MP_P1.00mm_Horizontal | 1 | Conn_01x08_Pin | C6074066
L1 | L_Bourns_SRP1245A | 1 | 10u | C840531
Q1 | Infineon-TG-TDSON-8-NMOS | 1 | N-ch, Vds>=60V, low Qgs | C3278729
Q2 | Infineon-TG-TDSON-8-NMOS | 1 | N-ch, Vds>=60V, low Rds | C501503
R1, R6 | 1206 | 2 | 1 | C2759212
R10 | 0402 | 1 | 120k | C144802
R11 | 2512 | 1 | 3.3 | C2960811
R12 | 0402 | 1 | 10k | C25744
R13, R25 | 0402 | 2 | 47k | C25792
R14 | 0402 | 1 | 110k | C138065
R15 | 0402 | 1 | 10k | C513708
R16, R19 | 0402 | 2 | 1k | C11702
R17 | 0402 | 1 | 240 | C852660
R18 | 0402 | 1 | 390 | C137997
R2 | 1206 | 1 | 5m | C7419996
R24 | 2512 | 1 | 1 | C3000711
R26 | 0402 | 1 | 4.3k | C852817
R3, R4 | 0402 | 2 | 10 | C25077
R5 | 0402 | 1 | 62k | C423271
R7 | 0402 | 1 | 2.7k | C423290
R8 | 0402 | 1 | 33k | C728559
R9 | 0402 | 1 | 82k | C852929
U1 | SOIC-8_3.9x4.9mm_P1.27mm | 1 | ADuM1200AR | C15219
U2 | TO-252-2 | 1 | LM317_DPAK | C68136
U3 | TSSOP-28-1EP_4.4x9.7mm_P0.65mm_EP2.74x4.75mm | 1 | LT3763 | C459912
U4 | TI-RDN0011A-MFG | 1 | TPSM365R6 | C6723000

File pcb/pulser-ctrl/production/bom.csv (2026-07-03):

Designator | Footprint | Quantity | Value | LCSC Part #
C1, C2 | 0402 | 2 | 1u | C52923
C3, C4, C5 | 0603 | 3 | 22u | C59461
C6, C7 | 0603 | 2 | 1u | C15849
D1 | 0603 | 1 | LED | C126319
D2 | 0603 | 1 | LED | C510024
D3 | 0603 | 1 | LED | C2286
J1 | JST_XH_S3B-XH-A_1x03_P2.50mm_Horizontal | 1 | I2C/XH | C48641715
J2, J4 | Molex_Connector_8pin_P1mm_526100872 | 2 | Conn_01x08_Pin | C588214
J3 | JST_XH_B2B-XH-AM_1x02_P2.50mm_Vertical | 1 | 36V IN | C42391660
J5 | PinSocket_1x02_P2.54mm_Vertical | 1 | Conn_01x02_Pin
PS1 | Converter_DCDC_Murata_MEE1SxxxxSC_THT | 1 | MEE1S0505SC | C7465178
R1 | 0402 | 1 | 100k | C25741
R2, R3, R4, R6 | 0402 | 4 | 10k | C25744
R5 | 0402 | 1 | 40.2k | C25893
R7 | 0402 | 1 | 15.8k | C26956
U1 | VQFN-20-1EP_3x3mm_P0.4mm_EP1.7x1.7mm | 1 | ATtiny1616-M | C507118
U2 | TI-RDN0011A-MFG | 1 | TPSM365R6 | C6723000

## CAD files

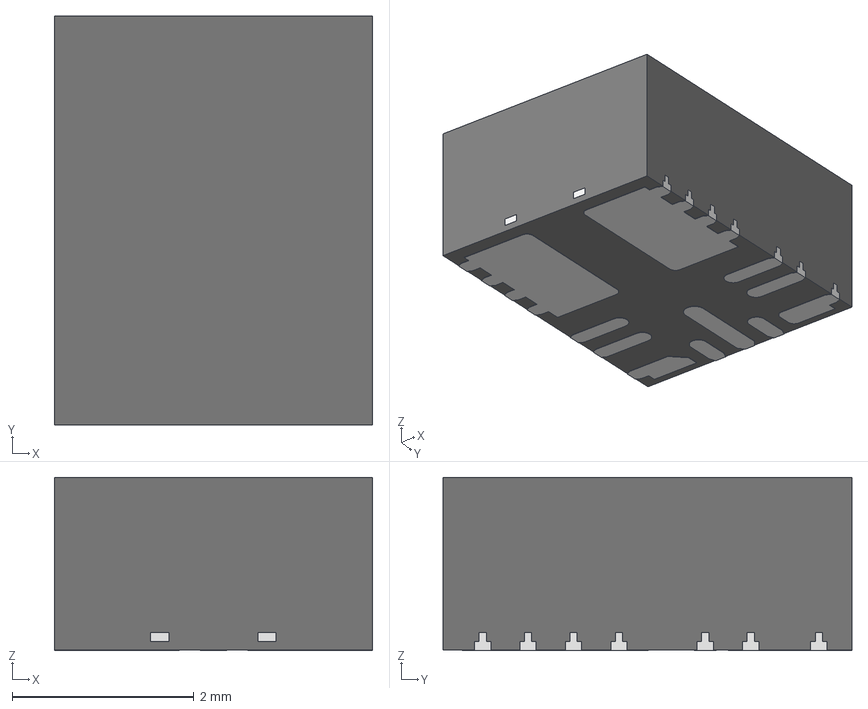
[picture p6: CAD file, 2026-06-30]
pcb/kicad/footprints/TI-RDN0011A.stp
3.50 x 4.50 x 1.91 mm
MOLD_CPOMPOUND_AF0
SOLID1-489_AF0
SOLID1-490_AF0
SOLID1-491_AF0
SOLID1-492_AF0
SOLID1-493_AF0
SOLID1-494_AF0
SOLID1-495_AF0
SOLID1-496_AF0
SOLID1-497_AF0
SOLID1-498_AF0

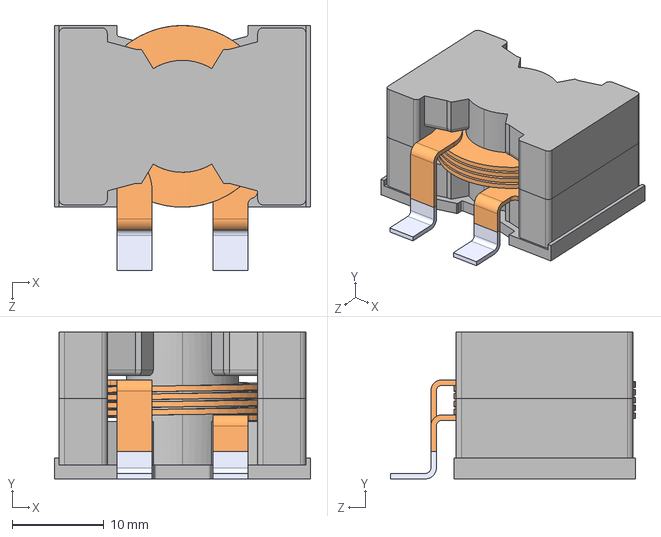
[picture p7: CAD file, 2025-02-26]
pcb/kicad/footprints/PQ2614B.step
27.9 x 16.0 x 26.7 mm

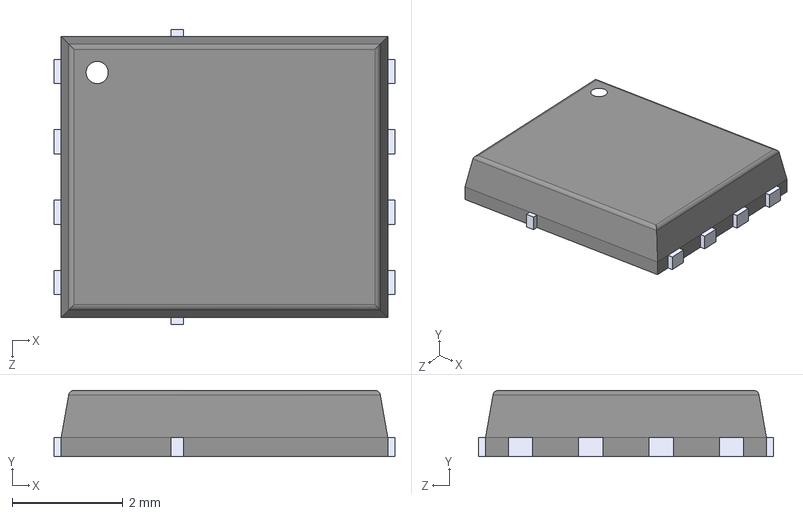
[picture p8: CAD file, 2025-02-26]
pcb/kicad/footprints/PG-TDSON-8.step
6.16 x 1.20 x 5.33 mm

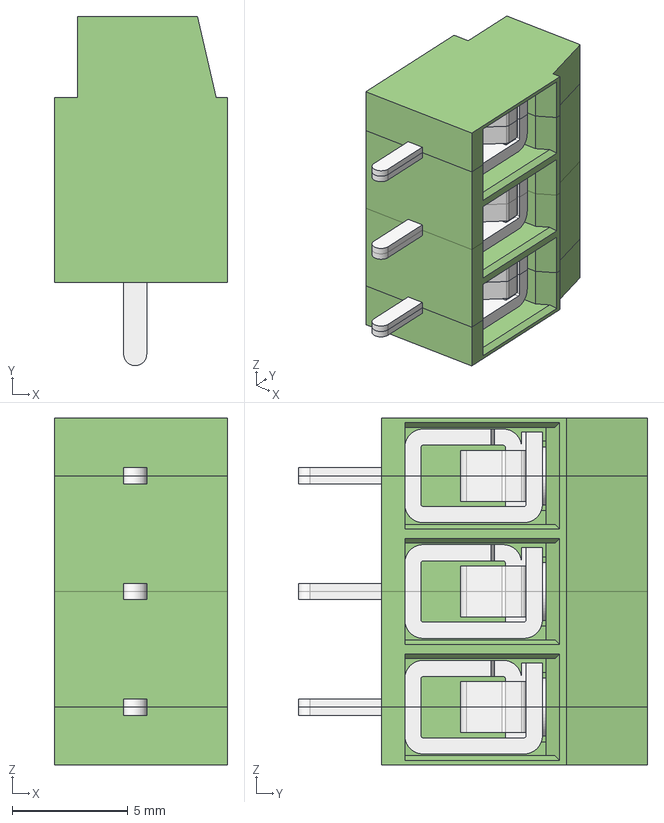
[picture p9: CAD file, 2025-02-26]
pcb/kicad/footprints/Wurth_TerminalBlock_3pin_P5mm_691137710003.stp
7.50 x 15.1 x 15.0 mm
MRT12P5_SX
MRT12P5_CNT x 2
MRT12P5_DX

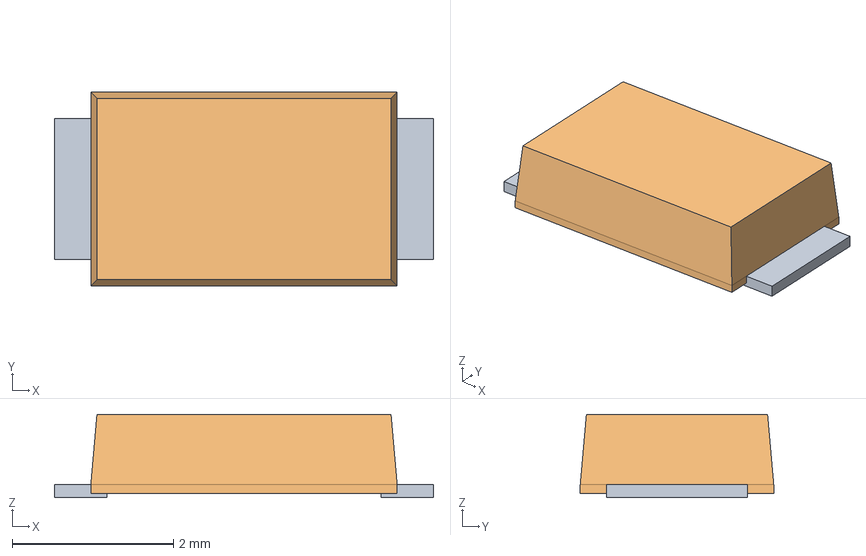
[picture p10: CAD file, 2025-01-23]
pcb/kicad/footprints/Toshiba_Diode_M-FLAT_3824.step
4.70 x 2.40 x 1.03 mm

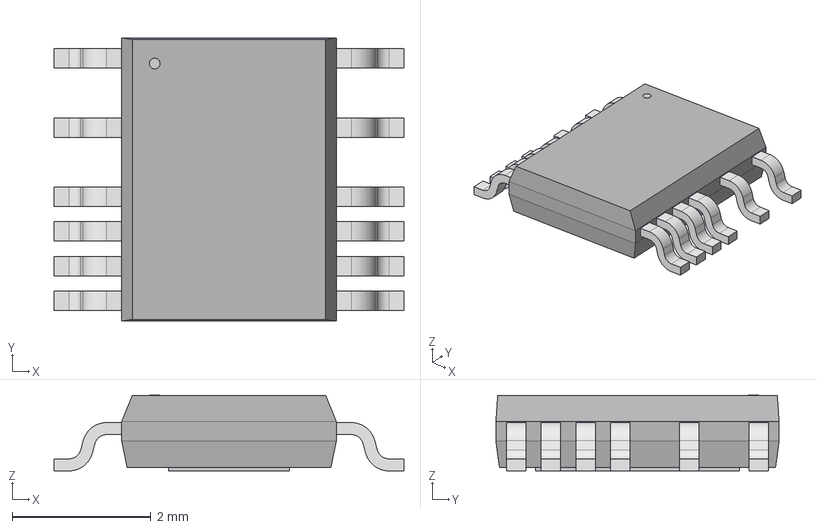
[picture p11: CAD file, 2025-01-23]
pcb/kicad/footprints/AD-MSOP-LT8365.step
5.05 x 4.09 x 1.09 mm

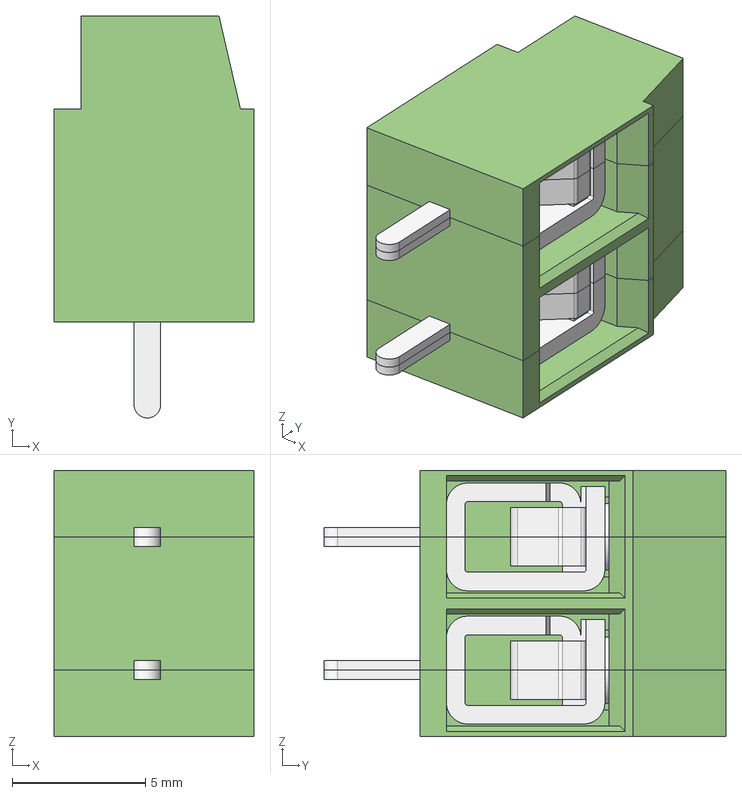
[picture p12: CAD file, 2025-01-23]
pcb/kicad/footprints/Wurth_TerminalBlock_2pin_P5mm_691137710002.stp
7.50 x 15.1 x 10.0 mm
MRT12P5_SX
MRT12P5_CNT
MRT12P5_DX

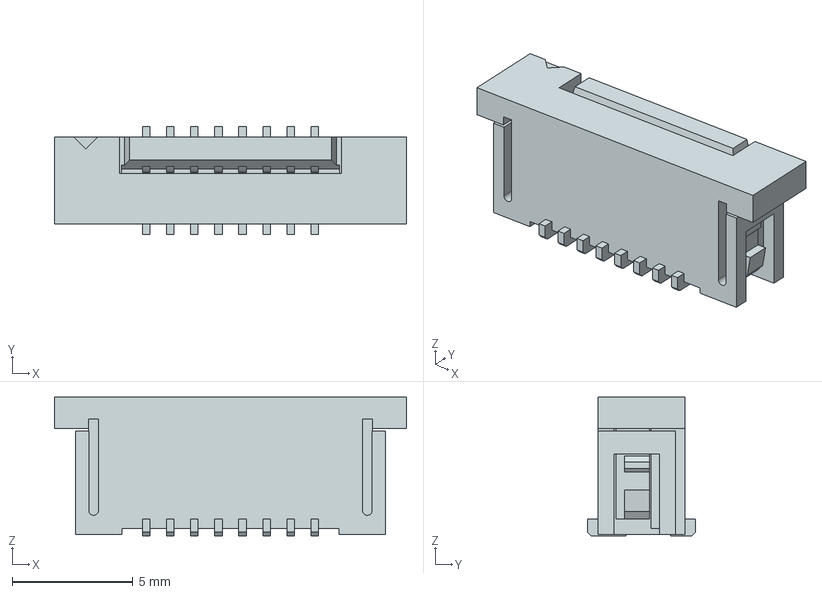
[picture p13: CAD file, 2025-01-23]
pcb/kicad/footprints/Molex_Connector_8pin_P1mm_526100872.step
14.6 x 4.50 x 5.75 mm

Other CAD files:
assy/assy-pulser.FCStd
assy/assy-ctrl.FCStd
assy/assy-pcbmod.FCStd
assy/assy-din.FCStd
assy/sheet-cover.FCStd
assy/ctrl-cover.FCStd
assy/mock-cover.FCStd
assy/frame.FCStd
assy/mock-terminals.FCStd
assy/mock-ctrl.FCStd
assy/dinbase.FCStd
assy/dinslide.FCStd
assy/duct.FCStd
assy/mock-fan.FCStd
assy/mock-heatsink.FCStd
assy/mock-pcb.FCStd
pcb/kicad/footprints/Bourns_Fuse_SF_6.1x2.6.step

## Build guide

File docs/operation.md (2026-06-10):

# Operation Model
Pulser operates in so-called "iso-pulse" mode (tries to keep pulse duration to configured value).
This docdescribes detailed timings & categorization.

When the device is running,
device activates in consecutive "windows".

windows

Each window is categorized into exactly 3 types.
Cooldown after window is determined by the type.

note: when device stops, window is immediately closed regardless of its type.

## Short Window

short window

When current started flowing too quickly (`Tig <= T_IG_SHORT`),
it's considered as a "short pulse", and window quickly terminates.

Cooldown will be `CD_SHORT`.

## Open Window

open window

When current doesn't start flowing after `T_IG_MAX`,
it's considered as "open".

## Good Window

good window

When current starts flowing at normal ignition delay `T_IG_SHORT <= Tig < T_IG_MAX`,
it's considered as an "good pulse", and active is held for pulse duration `Tdur`.

Since window duration of good pulse is determined by `Tig + Tdur`,
it can exceed `T_IG_MAX`.

Cooldown will be `max(CD_GOOD, cool_duty)`.

cooldown for good window

`cool_duty` is determined to satisfy `pulse_dur / (pulse_dur + cool_duty)` = `max_duty` config.

## Parameters

Ignition thresholds

* `T_IG_SHORT = 5us`
* `T_IG_MAX = 500us`

Cooldowns

* `CD_GOOD = 15us`: experimentally determined min value to de-arc properly
* `CD_SHORT = 100us`: has room to optimize. too short risks heatup due to de-arc failure
* `CD_OPEN = 500us`: big = less electrolysis but slower response

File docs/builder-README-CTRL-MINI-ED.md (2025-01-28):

# CTRL-MINI-ED (r1) Builder Manual

This doc is for people who want to build, modify, test ED board.
Current it's written for r1 (r0 didn't have any such doc).

## Assembly

You'll need the following
* PCBA-ed board
* heatsink
* 12V fan (2pin, XH connector)
* thermal sheet with electric isolation
* plastic M3 screw x2
* 220mΩ resistor & wire
* NTC 100kΩ free-hanging thermistor

Using these parts, you need to attach everything in one thermal block.

The termistor should be secured especially firmly,
because over-temperature protection depends on the thermistor reading.

The diode and the transistor's back plate may or may not be High-V.
Better to treat them as High-V, and apply isolation.
That way touching heatsink won't electrocute you.

## Test procedures

(Before tests)
Install external parts: current sense resistor, thermistor, heatsink, fan, Pico 2.

You should execute test groups sequentially. (i.e. execute _noconn only after _nofw is PASS)
Some tests don't make sense, or even dangerous, without preceding test groups.

### _nofw (No firmware)
Connect to 36V supply.

Tests:
* _nofw_led: LEDs = OFF
* _nofw_smoke: No smoke, max temp in thermography < 70℃ (Tamb<30℃) after 1 min
* _nofw_fan: fan = ON
* _nofw_pow: Power line voltages are nominal for:
  * _nofw_pow_uc: 5±0.5V (TP6), 3.3±0.5V (TP7)
  * _nofw_pow_dchg: 12±1V (TP5), 36±2V (TP26), 100±3V (TP25)
* _nofw_curr: Board current draw = 0.08±0.01A
* _nofw_out: GRINDER, WORK, TOOL = High-Z

### _nohost (No host connection)
Install firmware.

Tests:
* _nohost_led: Status LED = ON, Power LED = OFF
* _nohost_smoke: No smoke, max temp in thermography < 70℃ (Tamb<30℃) after 1 min

### _host (Host connection)
Connect to host. Host must be able to read/write registers.

Tests:
* _host_temp: Read TEMPERATURE. Must be within 5 degrees C of Tamb.
* _host_pol1: Write 1 to POLARITY. Relay switch sound, PWR(red)=ON, T=100V, W=0V, G=High-Z
* _host_pol2: Write 2 to POLARITY. Relay switch sound, PWR(red)=ON, T=0V, W=100V, G=High-Z
* _host_pol3: Write 3 to POLARITY. Relay switch sound, PWR(red)=ON, T=100V, W=High-Z, G=0V
* _host_pol4: Write 4 to POLARITY. Relay switch sound, PWR(red)=ON, T=0V, W=0V, G=100V
* _host_pol0: Write 0 to POLARITY. Relay switch sound, PWR(red)=OFF, T=High-Z, W=High-Z, G=High-Z

### _res (Resitive load)
Preparation
* Connect to host. Host must be able to read/write registers.
* Connect 12Ω load between Tool & Work.

Tests:
* _res_

100mA, 200mA
4A, 4.1A
7.9A, 8A

## Calibrations and other tweaks

## Real world measurements
Measurement procedures during actual EDM.

### _pulse
Prepare CTRL-MINI-ED, host controller, work & tool in operation fluid.

Trigger:
  M_GATE
  CURR_GATE
  CURR_DETECT
Current:
Voltage:

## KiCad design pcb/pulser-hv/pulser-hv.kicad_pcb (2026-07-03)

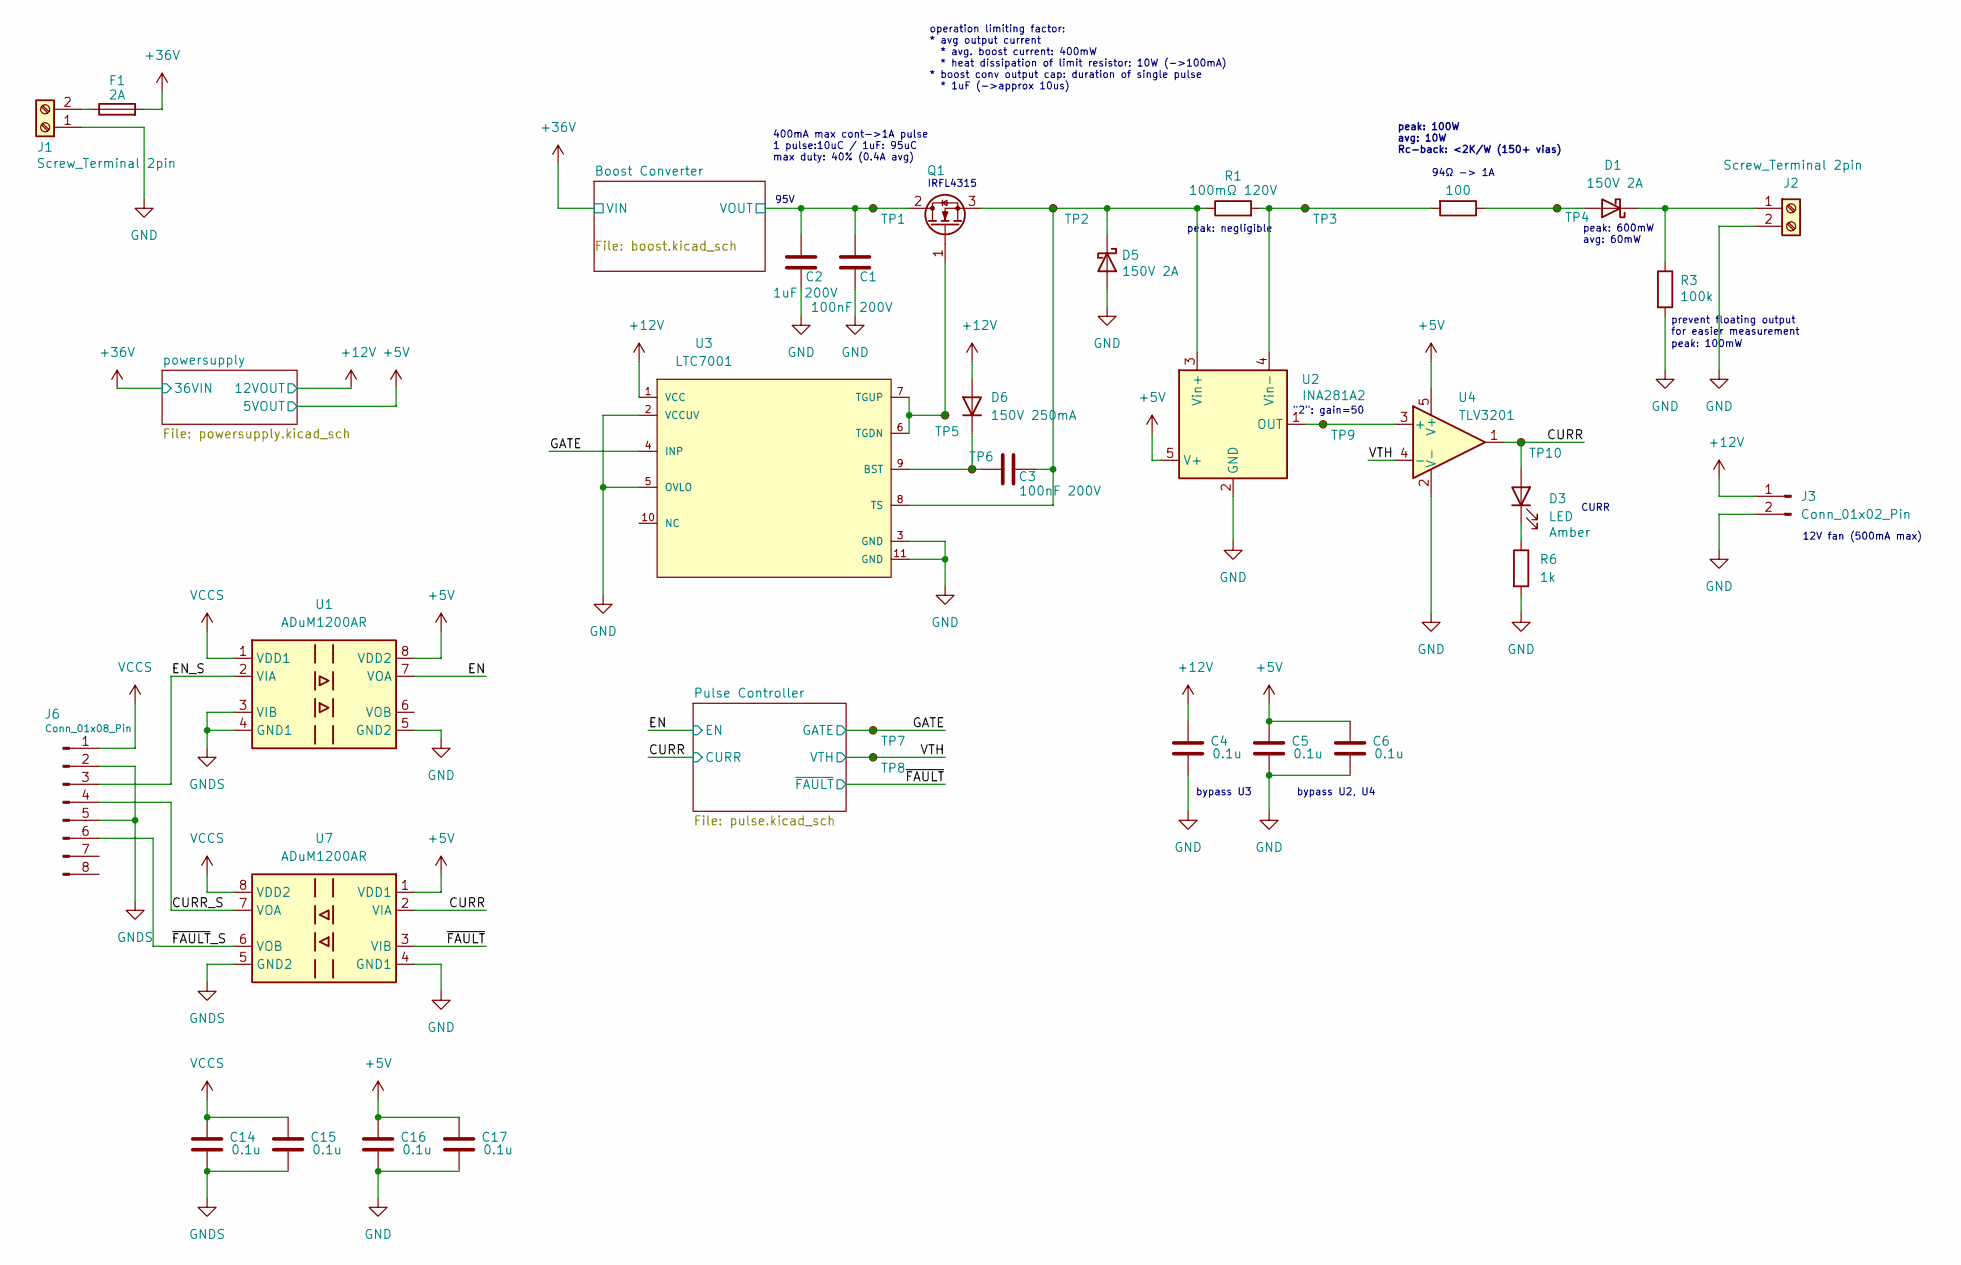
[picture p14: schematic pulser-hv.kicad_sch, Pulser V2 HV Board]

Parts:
C1, C3: 100nF 200V; C_1206_3216Metric; LCSC C113894
C2: 1uF 200V; C_1812_4532Metric; LCSC C3037685
C4, C5, C6: 0.1u; C_0603_1608Metric; LCSC C14663
C14, C15, C16, C17: 0.1u; C_0603_1608Metric
D1, D5: 150V 2A; D_SMC; LCSC C241922
D3: LED; LED_0603_1608Metric; Rating Amber; LCSC C165983
D6: 150V 250mA; D_TUMD2; LCSC C509964
F1: 2A; Fuse_Littelfuse-NANO2-451_453; LCSC C142852
J1, J2: Screw_Terminal 2pin; Wurth_TerminalBlock_2pin_P5mm_691137710002; LCSC C8269
J3: Conn_01x02_Pin; JST_XH_B2B-XH-A_1x02_P2.50mm_Vertical; LCSC C158012
J6: Conn_01x08_Pin; Molex_200528-0080_1x08-1MP_P1.00mm_Horizontal; LCSC C6074066
Q1: Q_NMOS_GDS; SOT-223-3_TabPin2; LCSC C537930
R1: 100mΩ 120V; R_1206_3216Metric; LCSC C25334
R3: 100k; R_1206_3216Metric; LCSC C17900
R4: 100; RESI-TO263; LCSC C37794578
R6: 1k; R_0603_1608Metric; LCSC C21190
TP1, TP2, TP3, TP4, TP5, TP6, TP7, TP8, TP9, TP10: TestPoint_Small; TestPoint_Pad_D1.5mm
U1, U7: ADuM1200AR; SOIC-8_3.9x4.9mm_P1.27mm; LCSC C15219
U2: INA281A2; SOT-23-5; LCSC C2908677
U3: LTC7001; MSOP-10-1EP_3x3mm_P0.5mm_EP1.68x1.88mm; LCSC C690094
U4: TLV3201; SOT-23-5; LCSC C105188

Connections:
+5V: C5.1, C6.1, C16.1, C17.1, U1.8 (VDD2), U2.5 (V+), U4.5 (V+), U7.1 (VDD1); also elsewhere on the board
+12V: C4.1, D6.2 (A), J3.1, U3.1 (VCC); also elsewhere on the board
+36V: F1.2; also elsewhere on the board
/Boost Converter/VOUT: C1.1, C2.1, Q1.2 (D), TP1.1; also elsewhere on the board
/CURR: D3.2 (A), TP10.1, U4.1, U7.2 (VIA); also elsewhere on the board
/CURR_S: J6.4, U7.7 (VOA)
/EN: U1.7 (VOA); also elsewhere on the board
/EN_S: J6.3, U1.2 (VIA)
/GATE: TP7.1, U3.4 (INP); also elsewhere on the board
/VTH: TP8.1, U4.4 (-); also elsewhere on the board
/~FAULT: U7.3 (VIB); also elsewhere on the board
/~FAULT_S: J6.6, U7.6 (VOB)
GND: C1.2, C2.2, C4.2, C5.2, C6.2, C16.2, C17.2, D5.2 (A), J1.1, J2.2, J3.2, R3.2, R4.3, R6.2, U1.5 (GND2), U2.2 (GND), U3.2 (VCCUV), U3.3 (GND), U3.5 (OVLO), U3.11 (GND), U4.2 (V-), U7.4 (GND1); also elsewhere on the board
GNDS: C14.2, C15.2, J6.2, J6.5, U1.3 (VIB), U1.4 (GND1), U7.5 (GND2)
unnamed: D1.2 (A), R4.1, TP4.1
unnamed: D1.1 (K), J2.1, R3.1
unnamed: D3.1 (K), R6.1
unnamed: C3.2, D5.1 (K), Q1.3 (S), R1.1, TP2.1, U2.3 (Vin+), U3.8 (TS)
unnamed: C3.1, D6.1 (K), TP6.1, U3.9 (BST)
unnamed: F1.1, J1.2
unnamed: Q1.1 (G), TP5.1, U3.6 (TGDN), U3.7 (TGUP)
unnamed: TP9.1, U2.1 (OUT), U4.3 (+)
unnamed: R1.2, R4.2, TP3.1, U2.4 (Vin-)
VCCS: C14.1, C15.1, J6.1, U1.1 (VDD1), U7.8 (VDD2)

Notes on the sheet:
CURR
bypass U2, U4
"2": gain=50
peak: 100W avg: 10W Rc-back: <2K/W (150+ vias)
peak: 600mW avg: 60mW
peak: 100mW
IRFL4315
95V
12V fan (500mA max)
94Ω -> 1A
peak: negligible
bypass U3
prevent floating output for easier measurement
operation limiting factor: * avg output current * avg. boost current: 400mW * heat dissipation of limit resistor: 10W (->100mA) * boost conv output cap: duration of single pulse * 1uF (->approx 10us)
400mA max cont->1A pulse 1 pulse:10uC / 1uF: 95uC max duty: 40% (0.4A avg)

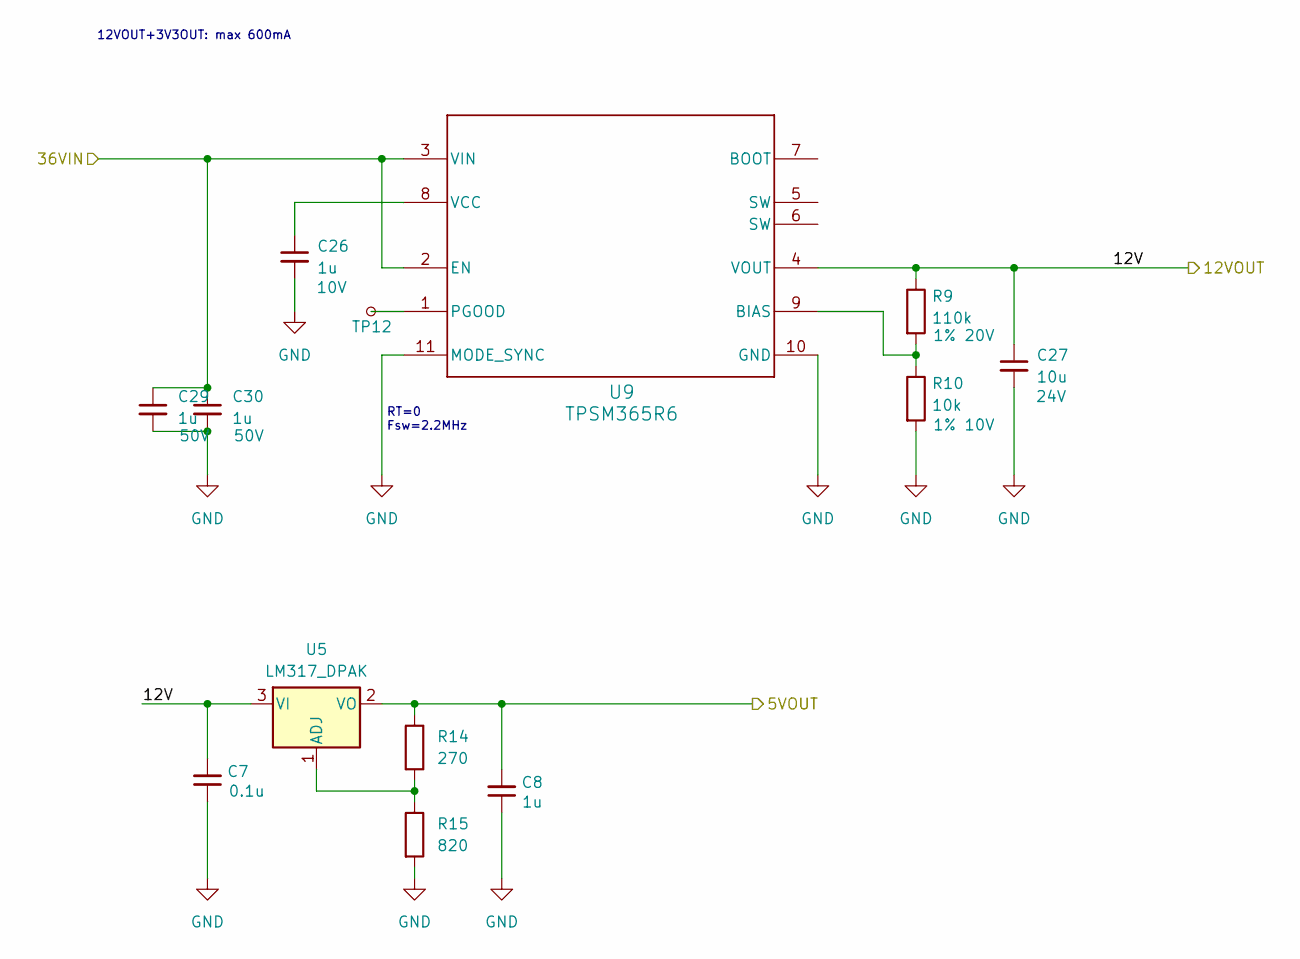
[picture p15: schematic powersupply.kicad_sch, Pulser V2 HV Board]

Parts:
C7: 0.1u; C_0603_1608Metric; LCSC C14663
C8: 1u; C_0603_1608Metric; LCSC C15849
C26: 1u; C_0402_1005Metric; Rating 10V; LCSC C52923
C27: 10u; C_0603_1608Metric; Rating 24V; LCSC C96446
C29, C30: 1u; C_0603_1608Metric; Rating 50V; LCSC C15849
R9: 110k; R_0402_1005Metric; Rating 1% 20V; LCSC C138065
R10: 10k; R_0402_1005Metric; Rating 1% 10V; LCSC C513708
R14: 270; R_0603_1608Metric; LCSC C22966
R15: 820; R_0603_1608Metric; LCSC C23253
TP12: TestPoint; TestPoint_Pad_D1.5mm
U5: LM317_DPAK; TO-252-2; LCSC C68136
U9: TPSM365R6; TI-RDN0011A-MFG; LCSC C6723000

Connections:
+5V: C8.2, R14.1, U5.2 (VO); also elsewhere on the board
+12V: C7.2, C27.1, R9.1, U5.3 (VI), U9.4 (VOUT); also elsewhere on the board
+36V: C29.1, C30.1, U9.2 (EN), U9.3 (VIN); also elsewhere on the board
GND: C7.1, C8.1, C26.2, C27.2, C29.2, C30.2, R10.2, R15.2, U9.10 (GND), U9.11 (MODE_SYNC); also elsewhere on the board
unnamed: R14.2, R15.1, U5.1 (ADJ)
unnamed: R9.2, R10.1, U9.9 (BIAS)
unnamed: TP12.1, U9.1 (PGOOD)
unnamed: C26.1, U9.8 (VCC)

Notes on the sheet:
RT=0 Fsw=2.2MHz
12VOUT+3V3OUT: max 600mA

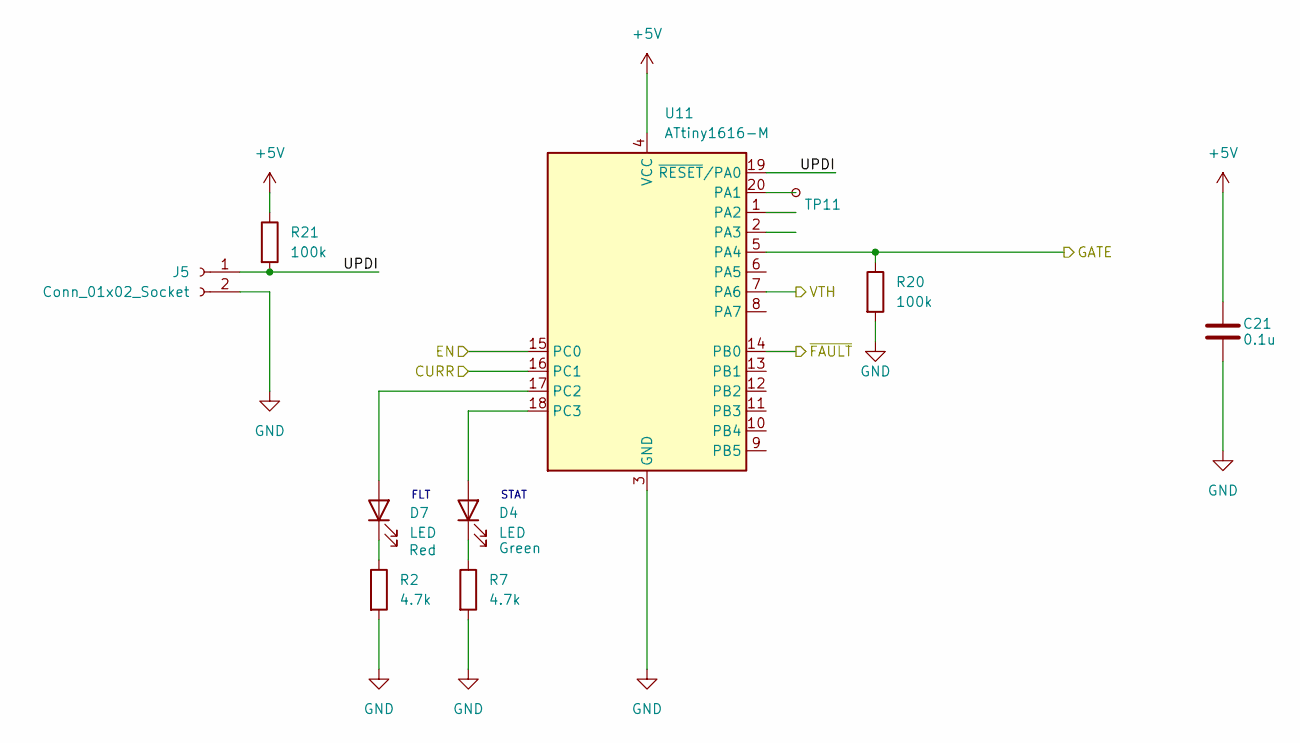
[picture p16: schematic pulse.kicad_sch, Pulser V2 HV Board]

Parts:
C21: 0.1u; C_0603_1608Metric; LCSC C14663
D4: LED; LED_0603_1608Metric; Rating Green; LCSC C126319
D7: LED; LED_0603_1608Metric; Rating Red; LCSC C2286
J5: Conn_01x02_Socket; PinSocket_1x02_P2.54mm_Vertical; LCSC C7499322
R2, R7: 4.7k; R_0603_1608Metric; LCSC C23162
R20, R21: 100k; R_0603_1608Metric; LCSC C25803
TP11: TestPoint_Small; TestPoint_Pad_D1.5mm
U11: ATtiny1616-M; VQFN-20-1EP_3x3mm_P0.4mm_EP1.7x1.7mm; LCSC C507118

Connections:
+5V: C21.2, R21.1, U11.4 (VCC); also elsewhere on the board
/CURR: U11.16 (PC1); also elsewhere on the board
/EN: U11.15 (PC0); also elsewhere on the board
/GATE: R20.1, U11.5 (PA4); also elsewhere on the board
/Pulse Controller/UPDI: J5.1, R21.2, U11.19 (~RESET/PA0)
/VTH: U11.7 (PA6); also elsewhere on the board
/~FAULT: U11.14 (PB0); also elsewhere on the board
GND: C21.1, J5.2, R2.2, R7.2, R20.2, U11.3 (GND), U11.21 (GND); also elsewhere on the board
unnamed: D4.2 (A), U11.18 (PC3)
unnamed: D4.1 (K), R7.1
unnamed: D7.2 (A), U11.17 (PC2)
unnamed: D7.1 (K), R2.1
unnamed: TP11.1, U11.20 (PA1)

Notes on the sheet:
FLT
STAT

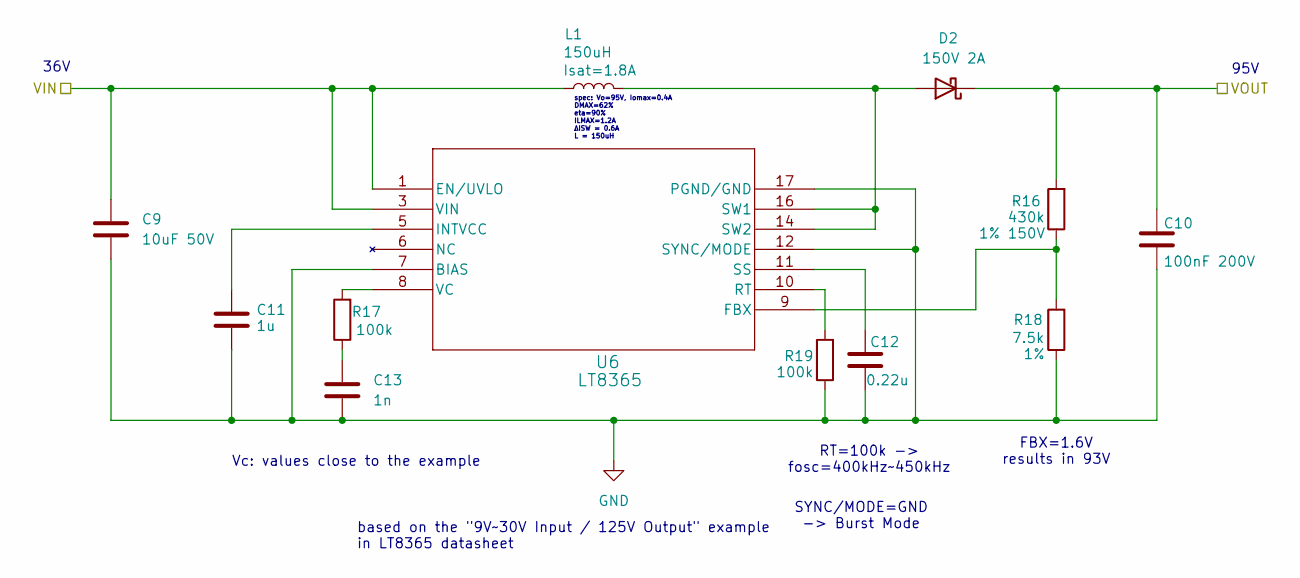
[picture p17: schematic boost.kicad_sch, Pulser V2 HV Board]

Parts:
C9: 10uF 50V; C_1206_3216Metric; LCSC C13585
C10: 100nF 200V; C_1206_3216Metric; LCSC C113894
C11: 1u; C_0603_1608Metric; LCSC C15849
C12: 0.22u; C_0603_1608Metric; LCSC C21120
C13: 1n; C_0603_1608Metric; LCSC C1588
D2: 150V 2A; D_SMC; LCSC C241922
L1: 150uH; L_12x12mm_H8mm; Rating Isat=1.8A; LCSC C338769
R16: 430k; R_1206_3216Metric; Rating 1% 150V
R17, R19: 100k; R_0603_1608Metric; LCSC C25803
R18: 7.5k; R_0603_1608Metric; Rating 1%; LCSC C23234
U6: LT8365; AD-MSOP-LT8365; LCSC C673785

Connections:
+36V: C9.1, L1.1, U6.1 (EN/UVLO), U6.3 (VIN); also elsewhere on the board
/Boost Converter/VOUT: C10.1, D2.1 (K), R16.2; also elsewhere on the board
GND: C9.2, C10.2, C11.2, C12.2, C13.2, R18.1, R19.1, U6.7 (BIAS), U6.12 (SYNC/MODE), U6.17 (PGND/GND); also elsewhere on the board
unnamed: C13.1, R17.1
unnamed: D2.2 (A), L1.2, U6.14 (SW2), U6.16 (SW1)
unnamed: R16.1, R18.2, U6.9 (FBX)
unnamed: C11.1, U6.5 (INTVCC)
unnamed: R19.2, U6.10 (RT)
unnamed: C12.1, U6.11 (SS)
unnamed: R17.2, U6.8 (VC)

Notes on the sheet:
Vc: values close to the example
RT=100k -> fosc=400kHz~450kHz
spec: Vo=95V, Iomax=0.4A DMAX=62% eta=90% ILMAX=1.2A ΔISW = 0.6A L = 150uH
FBX=1.6V results in 93V
95V
based on the "9V~30V Input / 125V Output" example in LT8365 datasheet
SYNC/MODE=GND -> Burst Mode
36V

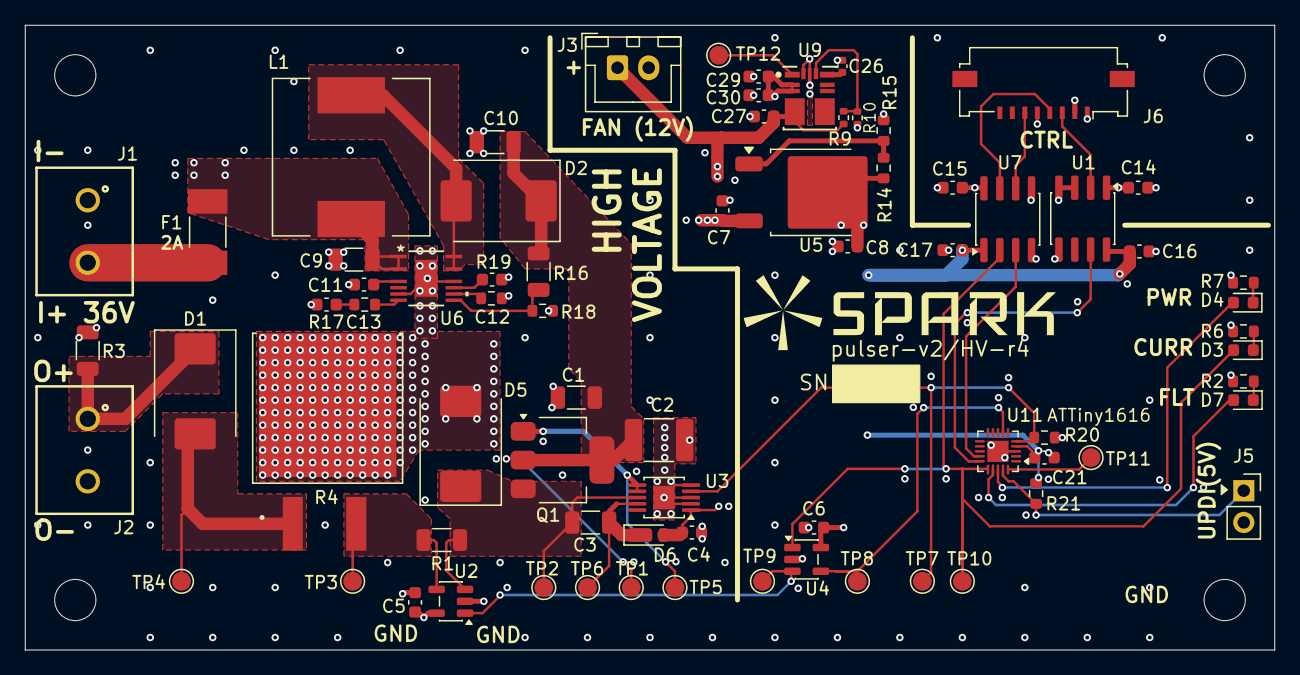
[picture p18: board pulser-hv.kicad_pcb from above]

Board: 4 copper layers, 100.0 x 50.0 mm, 74 parts (0 on the bottom side), 41 nets.

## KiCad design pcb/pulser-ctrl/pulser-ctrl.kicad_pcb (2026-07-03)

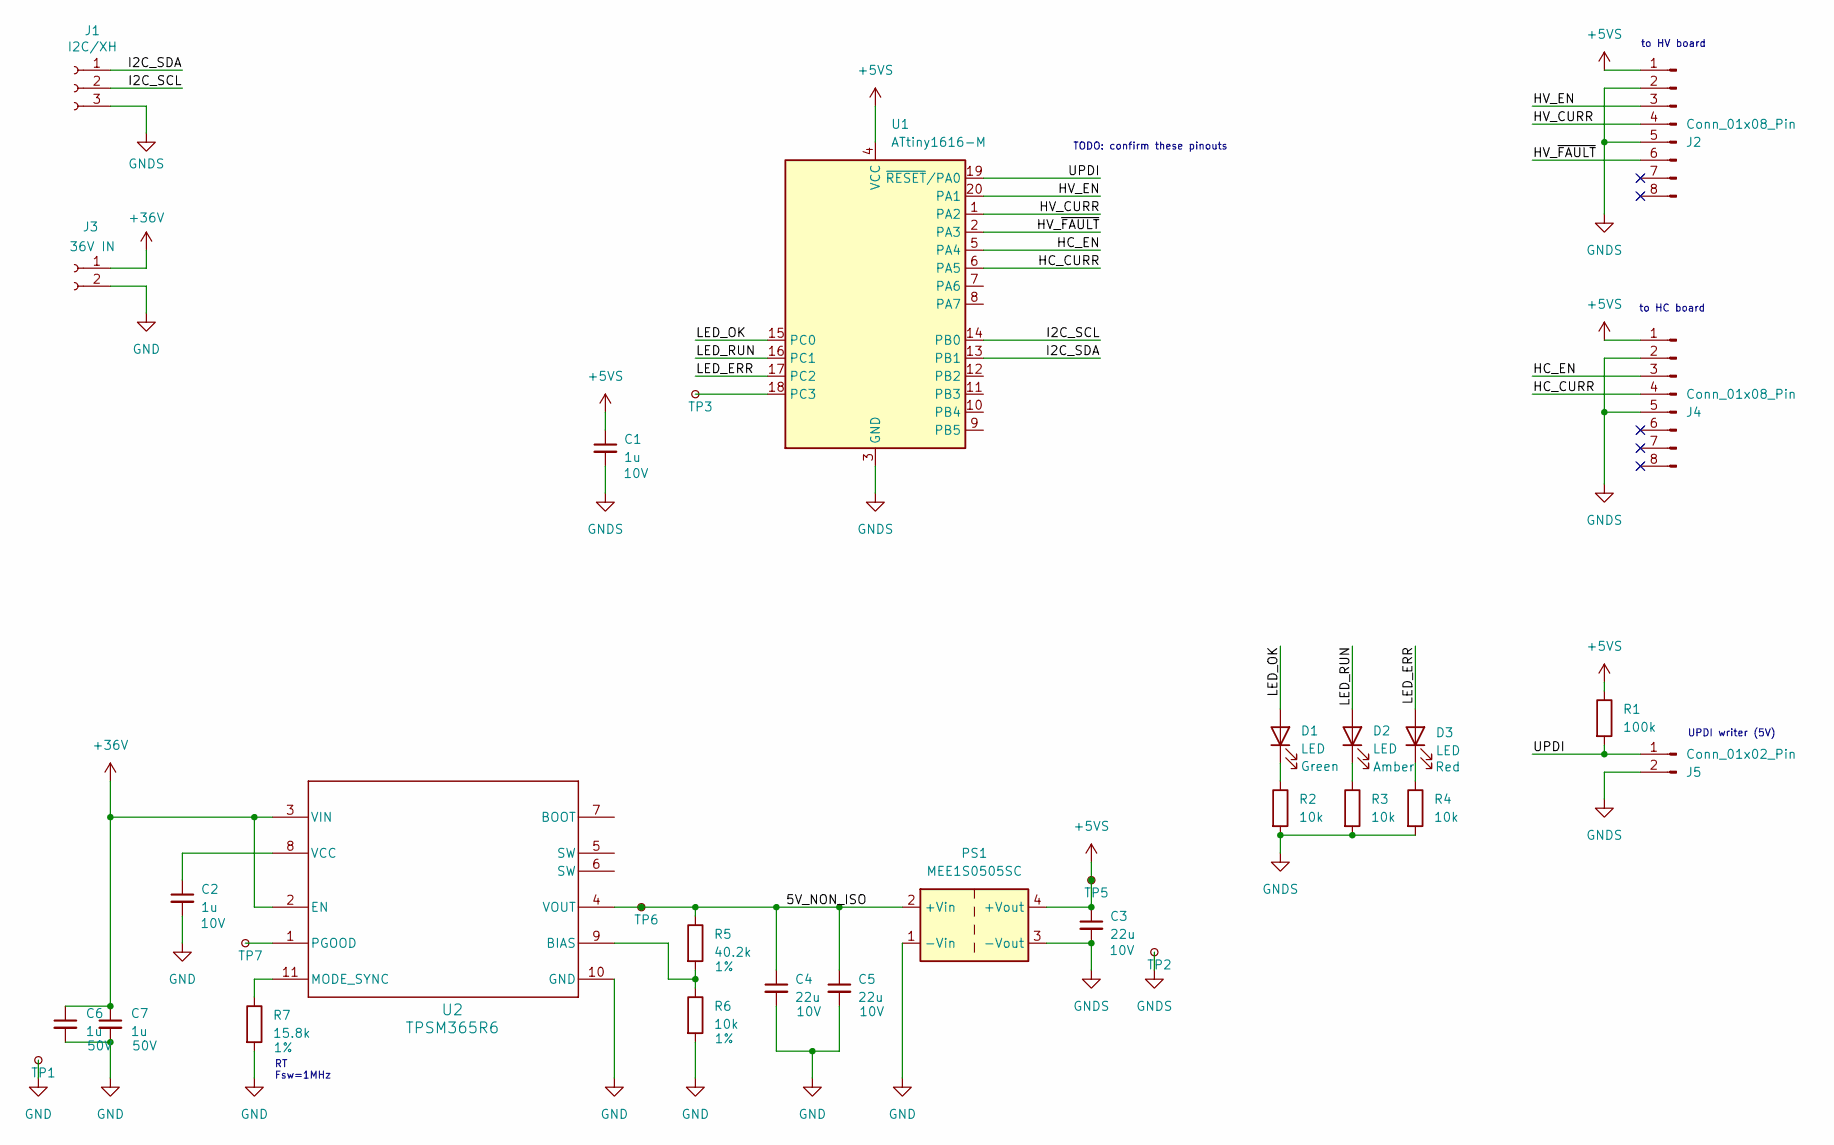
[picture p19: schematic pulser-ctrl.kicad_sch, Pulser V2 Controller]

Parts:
C1, C2: 1u; C_0402_1005Metric; Rating 10V; LCSC C52923
C3, C4, C5: 22u; C_0603_1608Metric; Rating 10V; LCSC C59461
C6, C7: 1u; C_0603_1608Metric; Rating 50V; LCSC C15849
D1: LED; LED_0603_1608Metric; Rating Green; LCSC C126319
D2: LED; LED_0603_1608Metric; Rating Amber; LCSC C510024
D3: LED; LED_0603_1608Metric; Rating Red; LCSC C2286
J1: I2C/XH; JST_XH_S3B-XH-A_1x03_P2.50mm_Horizontal; LCSC C48641715
J2, J4: Conn_01x08_Pin; Molex_Connector_8pin_P1mm_526100872; LCSC C588214
J3: 36V IN; JST_XH_B2B-XH-AM_1x02_P2.50mm_Vertical; LCSC C42391660
J5: Conn_01x02_Pin; PinSocket_1x02_P2.54mm_Vertical
PS1: MEE1S0505SC; Converter_DCDC_Murata_MEE1SxxxxSC_THT; LCSC C7465178
R1: 100k; R_0402_1005Metric; LCSC C25741
R2, R3, R4: 10k; R_0402_1005Metric; LCSC C25744
R5: 40.2k; R_0402_1005Metric; Rating 1%; LCSC C25893
R6: 10k; R_0402_1005Metric; Rating 1%; LCSC C25744
R7: 15.8k; R_0402_1005Metric; Rating 1%; LCSC C26956
TP1, TP2, TP3, TP5, TP6, TP7: TestPoint; TestPoint_Pad_D1.5mm
U1: ATtiny1616-M; VQFN-20-1EP_3x3mm_P0.4mm_EP1.7x1.7mm; LCSC C507118
U2: TPSM365R6; TI-RDN0011A-MFG; LCSC C6723000

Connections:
+5VS: C1.1, C3.1, J2.1, J4.1, PS1.4 (+Vout), R1.1, TP5.1, U1.4 (VCC)
+36V: C6.1, C7.1, J3.1, U2.2 (EN), U2.3 (VIN)
/5V_NON_ISO: C4.1, C5.1, PS1.2 (+Vin), R5.1, TP6.1, U2.4 (VOUT)
/HC_CURR: J4.4, U1.6 (PA5)
/HC_EN: J4.3, U1.5 (PA4)
/HV_CURR: J2.4, U1.1 (PA2)
/HV_EN: J2.3, U1.20 (PA1)
/HV_~FAULT: J2.6, U1.2 (PA3)
/I2C_SCL: J1.2, U1.14 (PB0)
/I2C_SDA: J1.1, U1.13 (PB1)
/LED_ERR: D3.2 (A), U1.17 (PC2)
/LED_OK: D1.2 (A), U1.15 (PC0)
/LED_RUN: D2.2 (A), U1.16 (PC1)
/UPDI: J5.1, R1.2, U1.19 (~RESET/PA0)
GND: C2.2, C4.2, C5.2, C6.2, C7.2, J3.2, PS1.1 (-Vin), R6.2, R7.2, TP1.1, U2.10 (GND)
GNDS: C1.2, C3.2, J1.3, J2.2, J2.5, J4.2, J4.5, J5.2, PS1.3 (-Vout), R2.2, R3.2, R4.2, TP2.1, U1.3 (GND), U1.21 (GND)
unnamed: D1.1 (K), R2.1
unnamed: D2.1 (K), R3.1
unnamed: D3.1 (K), R4.1
unnamed: TP3.1, U1.18 (PC3)
unnamed: R5.2, R6.1, U2.9 (BIAS)
unnamed: R7.1, U2.11 (MODE_SYNC)
unnamed: TP7.1, U2.1 (PGOOD)
unnamed: C2.1, U2.8 (VCC)

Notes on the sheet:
TODO: confirm these pinouts
to HC board
RT Fsw=1MHz
UPDI writer (5V)
to HV board

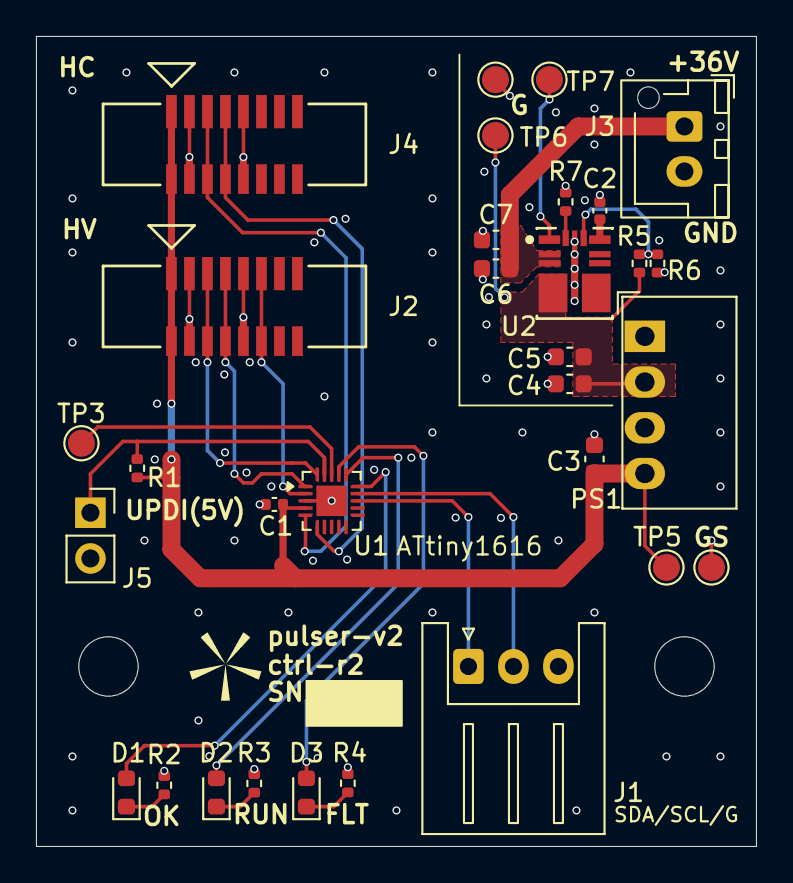
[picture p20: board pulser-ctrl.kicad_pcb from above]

Board: 4 copper layers, 40.0 x 45.0 mm, 31 parts (0 on the bottom side), 24 nets.

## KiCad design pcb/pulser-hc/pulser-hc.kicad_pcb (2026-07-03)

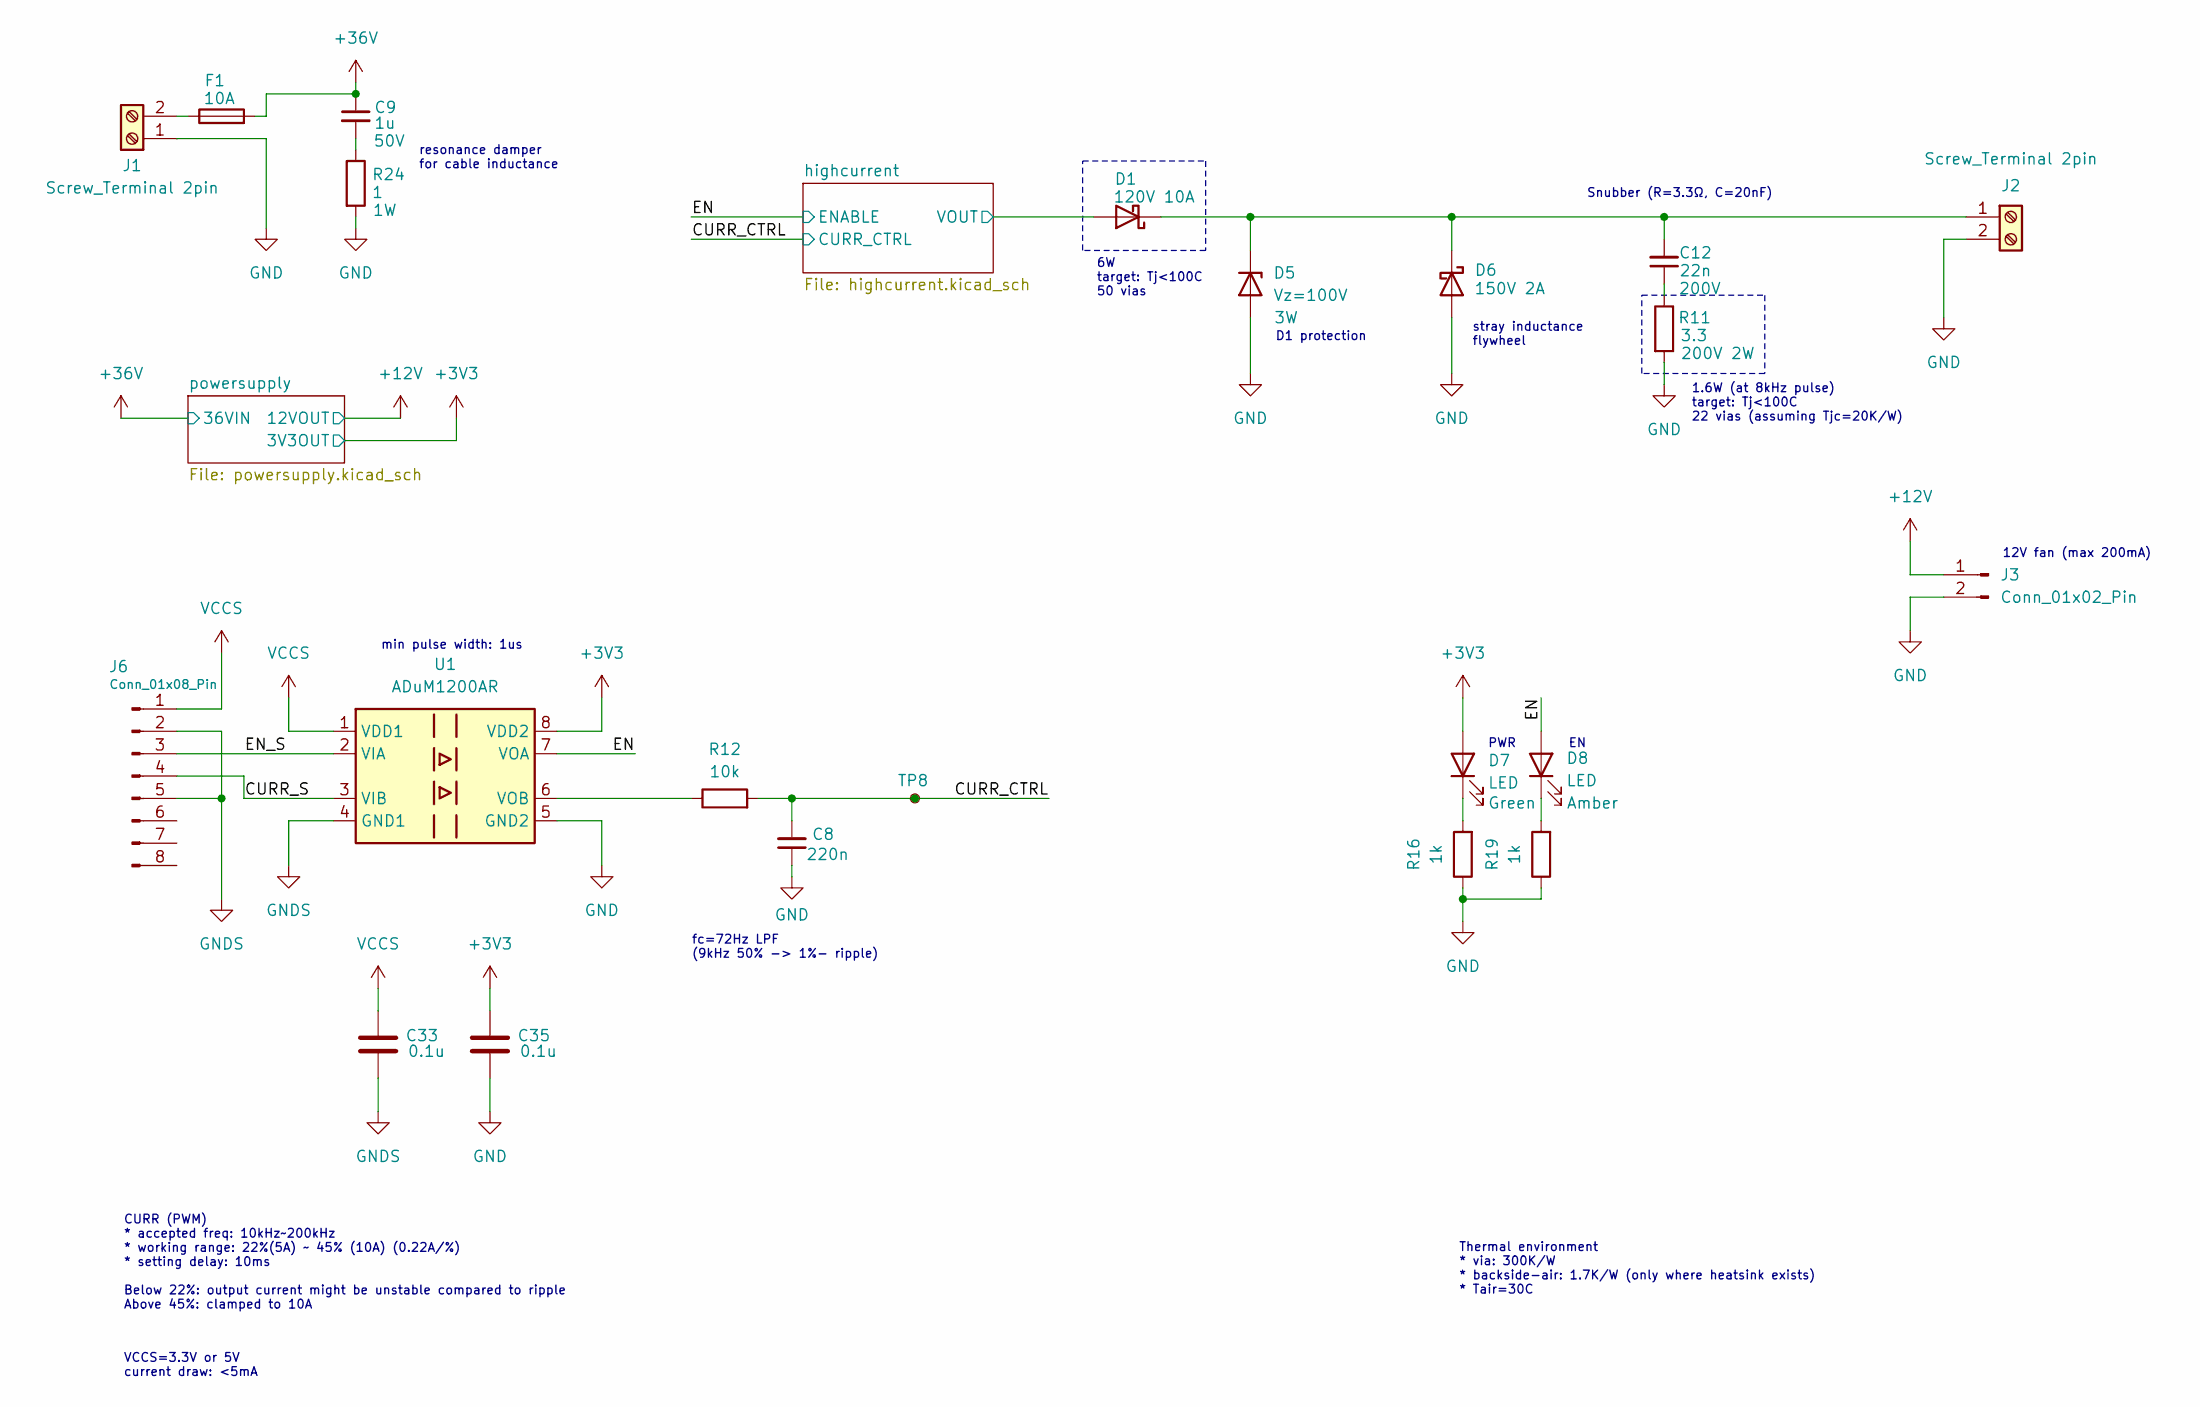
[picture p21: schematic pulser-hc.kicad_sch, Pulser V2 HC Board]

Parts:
C8: 220n; C_0603_1608Metric; Rating 10V; LCSC C21120
C9: 1u; C_0805_2012Metric; Rating 50V; LCSC C28323
C12: 22n; C_0805_2012Metric; Rating 200V; LCSC C5128361
C33, C35: 0.1u; C_0402_1005Metric; Rating 10V; LCSC C307331
D1: VISHAY-SMPC; Rating 120V 10A; LCSC C968542
D5: Vz=100V; D_SMB; Rating 3W; LCSC C150045
D6: TO-227A-2P; Rating 150V 2A; LCSC C2927414
D7: LED; LED_0805_2012Metric; Rating Green; LCSC C2297
D8: LED; LED_0805_2012Metric; Rating Amber; LCSC C5123498
F1: 10A; Fuse_Littelfuse-NANO2-451_453; LCSC C44479
J1, J2: Screw_Terminal 2pin; Wurth_TerminalBlock_2pin_P5mm_691137710002; LCSC C8269
J3: Conn_01x02_Pin; JST_XH_B2B-XH-A_1x02_P2.50mm_Vertical
J6: Conn_01x08_Pin; Molex_200528-0080_1x08-1MP_P1.00mm_Horizontal; LCSC C6074066
R11: 3.3; R_2512_6332Metric; Rating 200V 2W; LCSC C2960811
R12: 10k; R_0402_1005Metric; Rating 10V; LCSC C25744
R16, R19: 1k; R_0402_1005Metric; Rating 10V; LCSC C11702
R24: 1; R_2512_6332Metric; Rating 1W; LCSC C3000711
TP8: TestPoint; TestPoint_Pad_D1.5mm
U1: ADuM1200AR; SOIC-8_3.9x4.9mm_P1.27mm; LCSC C15219

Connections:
+3V3: C35.1, D7.2 (A), U1.8 (VDD2); also elsewhere on the board
+12V: J3.1; also elsewhere on the board
+36V: C9.1, F1.2; also elsewhere on the board
/CURR_CTRL: C8.2, R12.2, TP8.1; also elsewhere on the board
/CURR_S: J6.4, U1.3 (VIB)
/EN: D8.2 (A), U1.7 (VOA); also elsewhere on the board
/EN_S: J6.3, U1.2 (VIA)
/highcurrent/VOUT: D1.2 (A); also elsewhere on the board
GND: C8.1, C35.2, D5.2 (A), D6.2 (A), J1.1, J2.2, J3.2, R11.2, R16.1, R19.1, R24.2, U1.5 (GND2); also elsewhere on the board
GNDS: C33.2, J6.2, J6.5, U1.4 (GND1)
unnamed: C9.2, R24.1
unnamed: C12.1, R11.1
unnamed: C12.2, D1.1 (K), D5.1 (K), D6.1 (K), J2.1
unnamed: D7.1 (K), R16.2
unnamed: D8.1 (K), R19.2
unnamed: F1.1, J1.2
unnamed: R12.1, U1.6 (VOB)
VCCS: C33.1, J6.1, U1.1 (VDD1)

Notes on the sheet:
stray inductance flywheel
Snubber (R=3.3Ω, C=20nF)
VCCS=3.3V or 5V current draw: <5mA
fc=72Hz LPF (9kHz 50% -> 1%- ripple)
D1 protection
resonance damper for cable inductance
Thermal environment * via: 300K/W * backside-air: 1.7K/W (only where heatsink exists) * Tair=30C
6W target: Tj<100C 50 vias
min pulse width: 1us
CURR (PWM) * accepted freq: 10kHz~200kHz * working range: 22%(5A) ~ 45% (10A) (0.22A/%) * setting delay: 10ms Below 22%: output current might be unstable compared to ripple Above 45%: clamped to 10A
PWR
1.6W (at 8kHz pulse) target: Tj<100C 22 vias (assuming Tjc=20K/W)
12V fan (max 200mA)

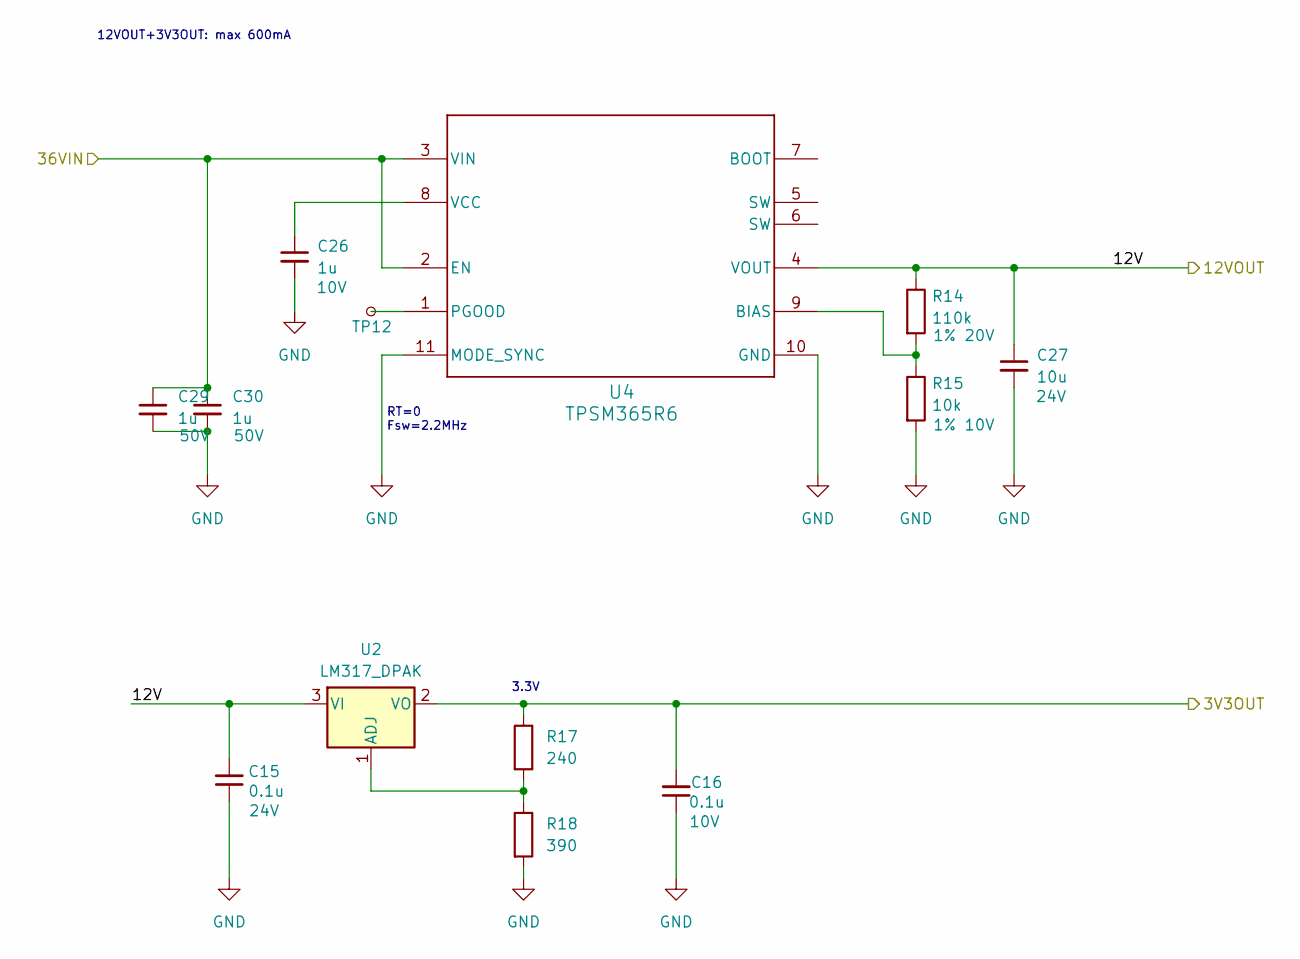
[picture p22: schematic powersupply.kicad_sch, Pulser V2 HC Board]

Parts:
C15: 0.1u; C_0402_1005Metric; Rating 24V; LCSC C307331
C16: 0.1u; C_0402_1005Metric; Rating 10V; LCSC C307331
C26: 1u; C_0402_1005Metric; Rating 10V; LCSC C52923
C27: 10u; C_0603_1608Metric; Rating 24V; LCSC C96446
C29, C30: 1u; C_0603_1608Metric; Rating 50V; LCSC C15849
R14: 110k; R_0402_1005Metric; Rating 1% 20V; LCSC C138065
R15: 10k; R_0402_1005Metric; Rating 1% 10V; LCSC C513708
R17: 240; R_0402_1005Metric; Rating 10V; LCSC C852660
R18: 390; R_0402_1005Metric; Rating 10V; LCSC C137997
TP12: TestPoint; TestPoint_Pad_D1.5mm
U2: LM317_DPAK; TO-252-2; LCSC C68136
U4: TPSM365R6; TI-RDN0011A-MFG; LCSC C6723000

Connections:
+3V3: C16.2, R17.1, U2.2 (VO); also elsewhere on the board
+12V: C15.2, C27.1, R14.1, U2.3 (VI), U4.4 (VOUT); also elsewhere on the board
+36V: C29.1, C30.1, U4.2 (EN), U4.3 (VIN); also elsewhere on the board
GND: C15.1, C16.1, C26.2, C27.2, C29.2, C30.2, R15.2, R18.2, U4.10 (GND), U4.11 (MODE_SYNC); also elsewhere on the board
unnamed: R17.2, R18.1, U2.1 (ADJ)
unnamed: R14.2, R15.1, U4.9 (BIAS)
unnamed: TP12.1, U4.1 (PGOOD)
unnamed: C26.1, U4.8 (VCC)

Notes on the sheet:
3.3V
12VOUT+3V3OUT: max 600mA
RT=0 Fsw=2.2MHz

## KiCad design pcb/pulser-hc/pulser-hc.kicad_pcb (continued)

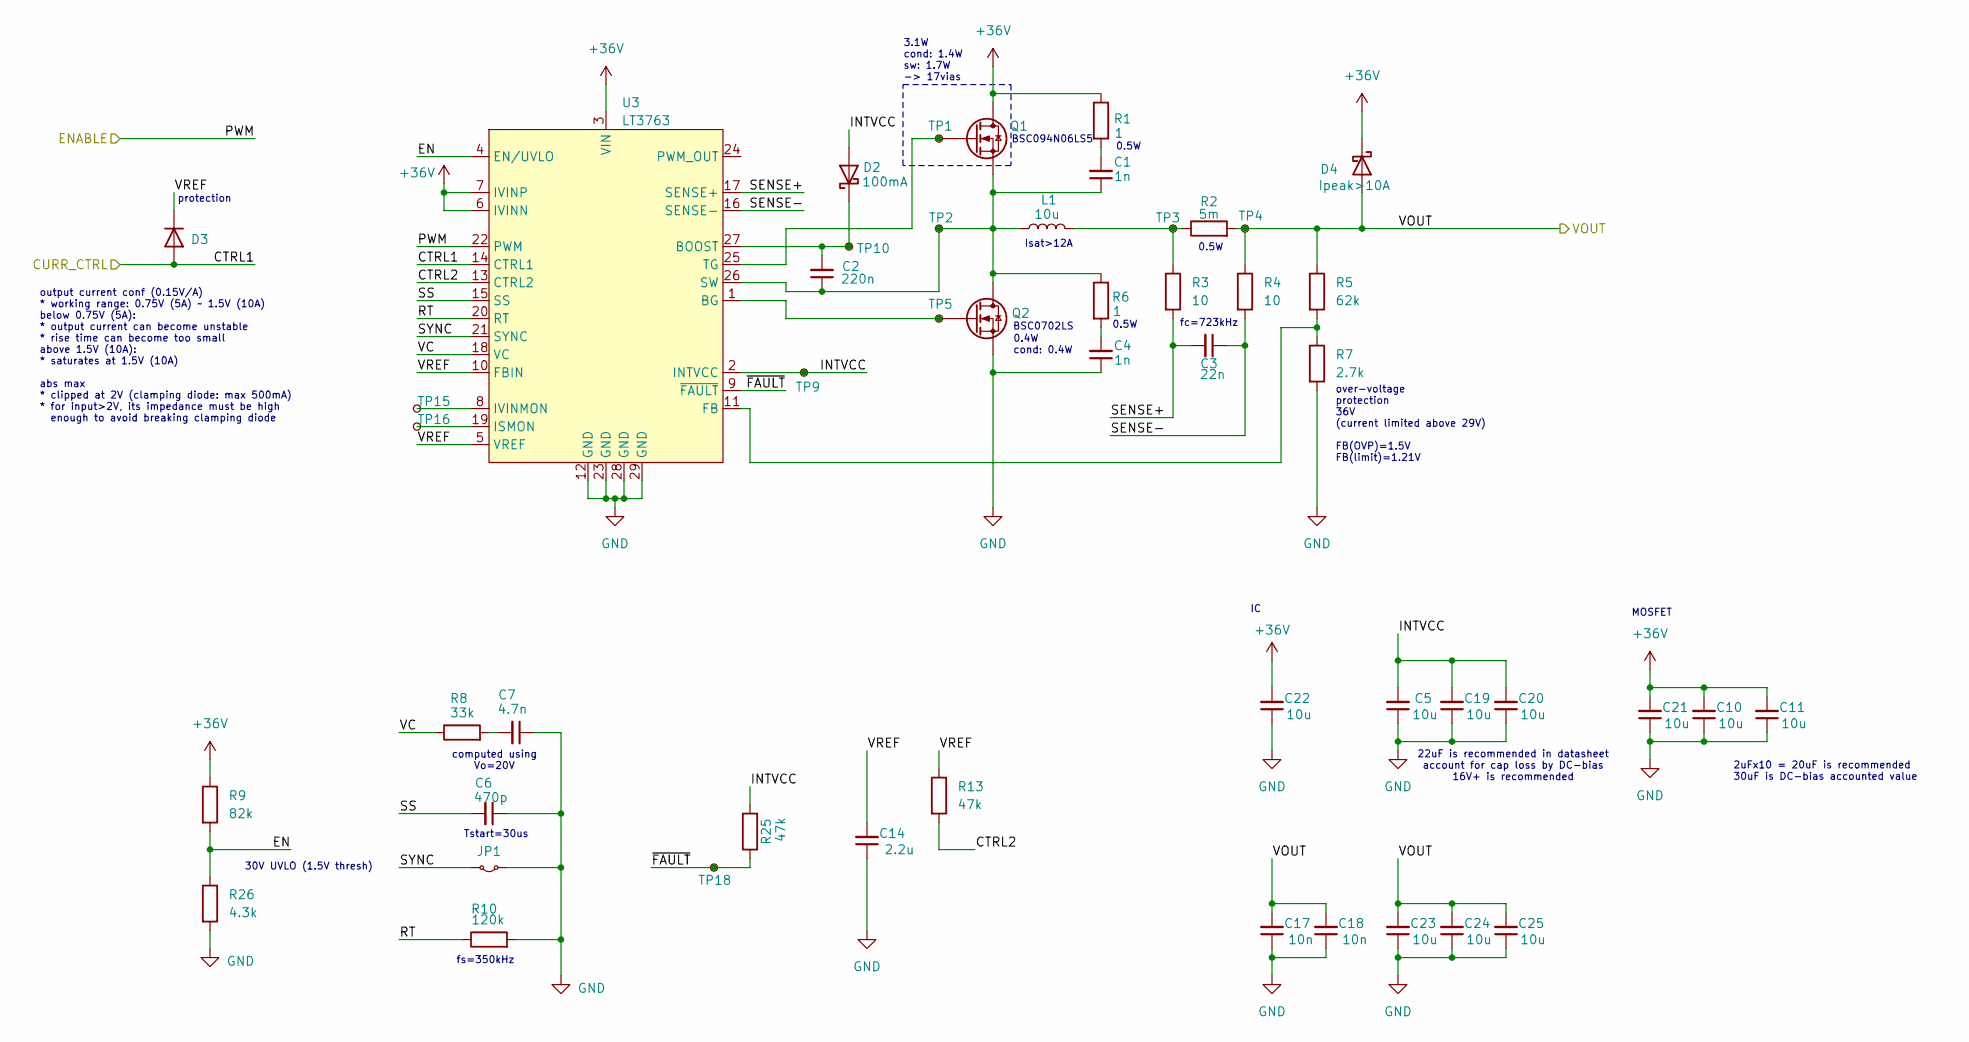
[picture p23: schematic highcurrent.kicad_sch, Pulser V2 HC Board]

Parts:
C1, C4: 1n; C_0402_1005Metric; Rating 50V; LCSC C1523
C2: 220n; C_0603_1608Metric; Rating 24V; LCSC C21120
C3: 22n; C_0402_1005Metric; Rating 10V; LCSC C1532
C5, C19, C20: 10u; C_0805_2012Metric; Rating 10V; LCSC C1713
C6: 470p; C_0402_1005Metric; Rating 10V; LCSC C26412
C7: 4.7n; C_0402_1005Metric; Rating 10V; LCSC C1538
C10, C11, C21, C23, C24, C25: 10u; C_1206_3216Metric; Rating 50V; LCSC C13585
C14: 2.2u; C_0603_1608Metric; Rating 10V; LCSC C23630
C17, C18: 10n; C_0402_1005Metric; Rating 50V; LCSC C15195
C22: 10u; C_1206_3216Metric; Rating 50V; LCSC C89632
D2: D_SOD-123; Rating 100mA; LCSC C177047
D3: D; D_SOD-123; Rating 500mA; LCSC C177047
D4: Ipeak>10A; TO-227A-2P; LCSC C2927414
JP1: Jumper_2_Small_Bridged; SolderJumper-2_P1.3mm_Bridged_RoundedPad1.0x1.5mm
L1: 10u; L_Bourns_SRP1245A; LCSC C840531
Q1: N-ch, Vds>=60V, low Qgs; Infineon-TG-TDSON-8-NMOS; LCSC C3278729
Q2: N-ch, Vds>=60V, low Rds; Infineon-TG-TDSON-8-NMOS; LCSC C501503
R1, R6: 1; R_1206_3216Metric; Rating 50V; LCSC C2759212
R2: 5m; R_1206_3216Metric; Rating 50V; LCSC C7419996
R3, R4: 10; R_0402_1005Metric; Rating 50V; LCSC C25077
R5: 62k; R_0402_1005Metric; Rating 50V; LCSC C423271
R7: 2.7k; R_0402_1005Metric; Rating 10V; LCSC C423290
R8: 33k; R_0402_1005Metric; Rating 10V; LCSC C728559
R9: 82k; R_0402_1005Metric; Rating 50V; LCSC C852929
R10: 120k; R_0402_1005Metric; Rating 10V; LCSC C144802
R13, R25: 47k; R_0402_1005Metric; Rating 10V; LCSC C25792
R26: 4.3k; R_0402_1005Metric; Rating 50V; LCSC C852817
TP1, TP2, TP3, TP4, TP5, TP9, TP10, TP15, TP16, TP18: TestPoint; TestPoint_Pad_D1.5mm
U3: LT3763; TSSOP-28-1EP_4.4x9.7mm_P0.65mm_EP2.74x4.75mm; LCSC C459912

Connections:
+36V: C10.2, C11.2, C21.2, C22.2, D4.1 (K), Q1.D, R1.1, R9.1, U3.3 (VIN), U3.6 (IVINN), U3.7 (IVINP); also elsewhere on the board
/CURR_CTRL: D3.2 (A), U3.14 (CTRL1); also elsewhere on the board
/EN: U3.22 (PWM); also elsewhere on the board
/highcurrent/CTRL2: R13.2, U3.13 (CTRL2)
/highcurrent/EN: R9.2, R26.1, U3.4 (EN/UVLO)
/highcurrent/INTVCC: C5.2, C19.2, C20.2, D2.2 (A), R25.2, TP9.1, U3.2 (INTVCC)
/highcurrent/RT: R10.1, U3.20 (RT)
/highcurrent/SENSE+: C3.2, R3.2, U3.17 (SENSE+)
/highcurrent/SENSE-: C3.1, R4.2, U3.16 (SENSE-)
/highcurrent/SS: C6.2, U3.15 (SS)
/highcurrent/SYNC: JP1.2 (B), U3.21 (SYNC)
/highcurrent/VC: R8.1, U3.18 (VC)
/highcurrent/VOUT: C17.2, C18.2, C23.2, C24.2, C25.2, D4.2 (A), R2.2, R4.1, R5.1, TP4.1; also elsewhere on the board
/highcurrent/VREF: C14.2, D3.1 (K), R13.1, U3.5 (VREF), U3.10 (FBIN)
/highcurrent/~FAULT: R25.1, TP18.1, U3.9 (~FAULT)
GND: C4.1, C5.1, C6.1, C7.1, C10.1, C11.1, C14.1, C17.1, C18.1, C19.1, C20.1, C21.1, C22.1, C23.1, C24.1, C25.1, JP1.1 (A), Q2.S, R7.2, R10.2, R26.2, U3.12 (GND), U3.23 (GND), U3.28 (GND), U3.29 (GND); also elsewhere on the board
unnamed: C1.2, R1.2
unnamed: C4.2, R6.2
unnamed: C7.2, R8.2
unnamed: C2.2, D2.1 (K), TP10.1, U3.27 (BOOST)
unnamed: L1.2, R2.1, R3.1, TP3.1
unnamed: Q2.G, TP5.1, U3.1 (BG)
unnamed: R5.2, R7.1, U3.11 (FB)
unnamed: TP16.1, U3.19 (ISMON)
unnamed: TP15.1, U3.8 (IVINMON)
unnamed: C1.1, C2.1, L1.1, Q1.S, Q2.D, R6.1, TP2.1, U3.26 (SW)
unnamed: Q1.G, TP1.1, U3.25 (TG)

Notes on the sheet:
0.5W
BSC094N06LS5
0.4W cond: 0.4W
protection
3.1W cond: 1.4W sw: 1.7W -> 17vias
22uF is recommended in datasheet account for cap loss by DC-bias 16V+ is recommended
2uFx10 = 20uF is recommended 30uF is DC-bias accounted value
fc=723kHz
over-voltage protection 36V (current limited above 29V) FB(OVP)=1.5V FB(limit)=1.21V
BSC0702LS
output current conf (0.15V/A) * working range: 0.75V (5A) ~ 1.5V (10A) below 0.75V (5A): * output current can become unstable * rise time can become too small above 1.5V (10A): * saturates at 1.5V (10A) abs max * clipped at 2V (clamping diode: max 500mA) * for input>2V, its impedance must be high e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
MOSFET
fs=350kHz
Isat>12A
computed using Vo=20V
30V UVLO (1.5V thresh)
Tstart=30us

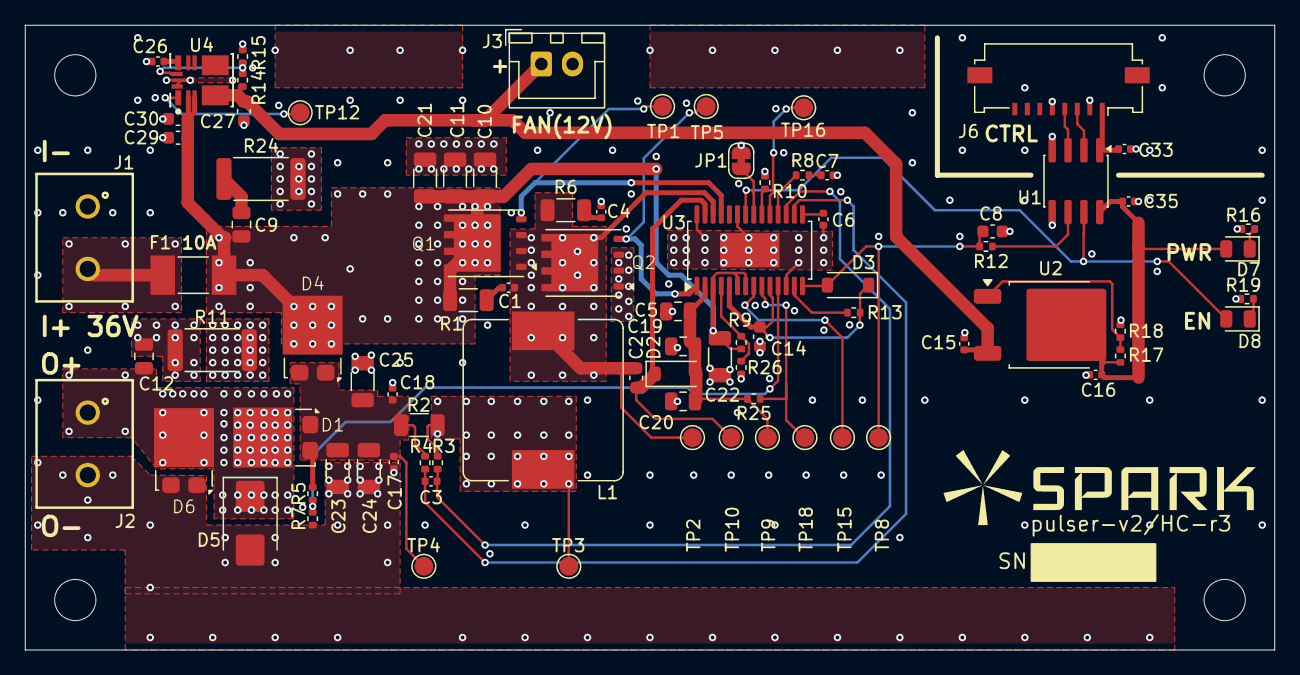
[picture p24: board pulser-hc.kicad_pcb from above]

Board: 4 copper layers, 100.0 x 50.0 mm, 85 parts (0 on the bottom side), 44 nets.

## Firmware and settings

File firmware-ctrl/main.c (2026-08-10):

// SPDX-License-Identifier: AGPL-3.0-or-later
/**
 * ATtiny1616 controller firmware. Device spec: register map
 * docs/i2c-registers.md, window model docs/operation.md.
 *
 * Single core:
 *   - The pulse loop runs in the foreground (main). It is the timing-critical
 *     path and must not be disrupted by more than ~1 us in-window.
 *   - The I2C slave runs in the TWI ISR; read_reg/write_reg execute there.
 *
 * Interrupts stay enabled throughout, including during a window, because every
 * ISR path that can fire while running is a handful of cycles:
 *   - Config writes are rejected while running (the !cfg_run guard), so the slow
 *     reclamp path never runs during cutting.
 *   - RES0's ratio math would be slow, so it is precomputed: the main loop keeps
 *     a "shadow" of the RES0/RES1 bytes (recompute_res, run out-of-window), and
 *     the ISR just returns it. Reading RES0 resets the WDT and clears the window
 *     counts; stats are only ever updated between windows.
 * A TWI byte interrupt that coincides with a timing edge therefore perturbs it
 * by at most one ISR (~2 us) and never cumulatively (bytes are >=25 us apart at
 * 400 kHz, and busy-waits are referenced to the free-running TCB0, so pulse
 * width stays exact regardless of interrupts). No multi-ms clock stretching.
 *
 * Shared state needs no locks beyond brief ATOMIC_BLOCK guards on the multi-byte
 * values the ISR and pulse loop both touch (cfg_wdt_ref, stat counts).
 */
#define F_CPU 20000000UL

#include <avr/cpufunc.h>
#include <avr/interrupt.h>
#include <avr/io.h>
#include <stdbool.h>
#include <stdint.h>
#include <util/atomic.h>
#include "config.h"

static const uint8_t MODE_PROBE = 0;  // cut mode is the complementary value 1

// Permanent fault: sticky, set by HV_FAULT or the boot self-test. The device
// cannot run while set and there is no way to clear it (FAULT.fault is a no-op).
static volatile bool fault = false;

// Config + run control. Written by the TWI ISR (host) and by the pulse loop;
// read by the pulse loop each iteration. `run` is bidirectional: the host
// starts/stops it, the device clears it on probe completion or WDT timeout.
static volatile bool cfg_run = false;
static volatile bool cfg_wdt = false;             // WDT timeout latched; host clears via FAULT
static volatile bool cfg_probe_detected = false;  // probe-mode conduction result
static volatile uint16_t cfg_wdt_ref = 0;         // TCA0.CNT at last RES0 read / run start
static volatile uint8_t cfg_mode = 0;
// Register values, clamped to the active current's operating range at write time
// and kept self-consistent across the CURR->DUR->DUTY dependency chain (see
// reclamp_dur / reclamp_duty), so reads always return in-range values.
static volatile uint8_t cfg_curr = 0;  // supported current (A): 1 or 10
static volatile uint8_t cfg_dur = 0;   // DUR register byte: | reserved:1 | exp:2 | frac:5 |
static volatile uint8_t cfg_duty = 0;  // DUTY register byte: max duty = (cfg_duty + 1)/256

// Cut-mode window counts since last RES0 read: incremented by the pulse loop
// (between windows, under ATOMIC_BLOCK), zeroed by the ISR on RES0 read and on
// run-start. The WDT caps the reset interval at ~51 ms and the fastest window is
// tens of microseconds, so each count stays within uint16.
static volatile uint16_t stat_open = 0;
static volatile uint16_t stat_short = 0;
static volatile uint16_t stat_good = 0;

// Precomputed RES0/RES1 bytes ("if RES0 were read now"). The main loop refreshes
// these out-of-window (recompute_res); the ISR returns them so the RES0 handler
// stays a few cycles. res0_shadow excludes the fault bit, which the ISR ORs in
// live. See docs/i2c-registers.md.
static volatile uint8_t res0_shadow = 0;
static volatile uint8_t res1_shadow = 0;

// Supported pulse currents (A) and their operating ranges. See
// docs/i2c-registers.md "operational range".
static const uint8_t CURR_1A = 1;    // exercises HV module only
static const uint8_t CURR_10A = 10;  // HV ignites, HC carries the pulse

// 10 A duration band (us). Pulses >= DUR_10A_LONG_US get the higher duty cap.
static const uint32_t DUR_10A_MIN_US = 25;
static const uint32_t DUR_10A_MAX_US = 950;
static const uint32_t DUR_10A_LONG_US = 100;
// 1 A duration is fixed by the HV firmware (HV-only pulse).
static const uint32_t DUR_1A_US = 10;

// Max duty as a DUTY register code (duty = (code + 1)/256), floored so the
// effective duty never exceeds the rated percentage.
static const uint8_t DUTY_MIN_CODE = 2;        // ~1%
static const uint8_t DUTY_1A_MAX = 22;         // ~9%
static const uint8_t DUTY_10A_SHORT_MAX = 47;  // ~19% (25..95us band)
static const uint8_t DUTY_10A_LONG_MAX = 124;  // ~49% (100..950us band)

static const uint8_t MODE_ON_RESET = 0x00;  // probe
static const uint8_t CURR_ON_RESET = 0x0a;  // 10 A
static const uint8_t DUR_ON_RESET = 0x42;   // 100 us
static const uint8_t DUTY_ON_RESET = 0x7c;  // ~49% (10 A long-band max)

// Clamp a current request to the nearest supported value (1 A or 10 A).
static uint8_t clamp_curr(uint8_t req) {
  return req <= (CURR_1A + CURR_10A) / 2 ? CURR_1A : CURR_10A;
}

// Decode a DUR register byte to pulse duration (us). exp==3 and frac 20..31 are
// reserved; treat them as the largest in-range code so a stray write maps to the
// longest scale rather than zero.
static uint32_t dur_decode_us(uint8_t b) {
  uint8_t exp = (b >> 5) & 0x03;
  uint8_t frac = b & 0x1f;
  if (exp > 2) {
    exp = 2;
  }
  if (frac > 19) {
    frac = 19;
  }
  uint32_t mul = exp == 0 ? 10u : (exp == 1 ? 100u : 1000u);
  return mul * frac / 20u;
}

// Encode a pulse duration (us) back to a canonical DUR byte (smallest exp).
static uint8_t dur_encode(uint32_t us) {
  for (uint8_t exp = 0; exp <= 2; exp++) {
    uint32_t mul = exp == 0 ? 10u : (exp == 1 ? 100u : 1000u);
    uint32_t frac = us * 20u / mul;
    if (frac >= 1 && frac <= 19 && mul * frac / 20u == us) {
      return (uint8_t)((exp << 5) | frac);
    }
  }
  return 0;  // unreachable: every clamped duration is representable
}

// Clamp pulse duration to the operating range of the active current.
static uint32_t clamp_dur_us(uint8_t curr, uint32_t us) {
  if (curr == CURR_1A) {
    return DUR_1A_US;  // fixed by HV firmware
  }
  if (us < DUR_10A_MIN_US) {
    return DUR_10A_MIN_US;
  }
  if (us > DUR_10A_MAX_US) {
    return DUR_10A_MAX_US;
  }
  return us;
}

// Clamp a DUTY register code to the band allowed by the active current &
// (already-clamped) duration.
static uint8_t clamp_duty_code(uint8_t curr, uint32_t dur_us, uint8_t code) {
  uint8_t hi;
  if (curr == CURR_1A) {
    hi = DUTY_1A_MAX;
  } else {
    hi = dur_us >= DUR_10A_LONG_US ? DUTY_10A_LONG_MAX : DUTY_10A_SHORT_MAX;
  }
  if (code < DUTY_MIN_CODE) {
    return DUTY_MIN_CODE;
  }
  if (code > hi) {
    return hi;
  }
  return code;
}

// Re-clamp the stored DUTY into the band allowed by the current CURR & DUR.
static void reclamp_duty() {
  cfg_duty = clamp_duty_code(cfg_curr, dur_decode_us(cfg_dur), cfg_duty);
}

// Re-clamp the stored DUR into the current CURR's range (canonicalizing the
// byte), then re-clamp DUTY since its band depends on DUR.
static void reclamp_dur() {
  cfg_dur = dur_encode(clamp_dur_us(cfg_curr, dur_decode_us(cfg_dur)));
  reclamp_duty();
}

////////////////////////////////////////////////////////////////////////////////
// Register read/write & TWI slave (runs in the TWI ISR).

enum {
  REG_CTRL = 0x01,
  REG_MODE = 0x02,
  REG_CURR = 0x03,
  REG_DUR = 0x04,
  REG_DUTY = 0x05,
  REG_RES0 = 0x08,
  REG_RES1 = 0x09,
  REG_FAULT = 0x10,
};

// num_good captured at the last RES0 read, returned by the following RES1 read.
// Lets the host fetch (RES0, RES1) atomically via a sequential read.
static uint8_t res1_latch = 0;

static bool i2c_ptr_written = false;
static uint8_t i2c_reg_ptr = 0;

// True until the first transmitted byte of the current read segment. RXACK
// latches the master's most recent ACK bit across transactions, so it is only
// meaningful for the second and later bytes of a slave transmit.
static bool i2c_tx_first = false;

// Called from the TWI ISR (interrupts off); no extra locking needed.
static void write_reg(uint8_t reg, uint8_t val) {
  switch (reg) {
    case REG_CTRL: {
      bool run_req = val & 0x01;
      if (!run_req) {
        cfg_run = false;
      } else if (!cfg_run && !fault) {
        // Rising edge of run: arm WDT and clear last run's results. A latched
        // wdt bit does not block restart; it is recoverable, unlike fault.
        cfg_run = true;
        cfg_wdt_ref = TCA0.SINGLE.CNT;
        cfg_probe_detected = false;
        stat_open = stat_short = stat_good = 0;
      }
      break;
    }
    case REG_MODE:
      if (!cfg_run) {  // write fails while running
        cfg_mode = val & 0x01;
      }
      break;
    case REG_CURR:
      if (!cfg_run) {
        cfg_curr = clamp_curr(val);
        reclamp_dur();  // DUR (and DUTY) band depends on CURR
      }
      break;
    case REG_DUR:
      if (!cfg_run) {
        cfg_dur = val;
        reclamp_dur();  // clamp/canonicalize DUR, then re-clamp DUTY
      }
      break;
    case REG_DUTY:
      if (!cfg_run) {
        cfg_duty = val;
        reclamp_duty();
      }
      break;
    case REG_FAULT:
      if (val & 0x02) {  // wdt bit: write 1 clears
        cfg_wdt = false;
      }
      // fault bit write is a no-op.
      break;
  }
}

// Called from the TWI ISR (interrupts off); no extra locking needed.
static uint8_t read_reg(uint8_t reg) {
  switch (reg) {
    case REG_CTRL:
      return cfg_run ? 1 : 0;
    case REG_MODE:
      return cfg_mode;
    case REG_CURR:
      return cfg_curr;
    case REG_DUR:
      return cfg_dur;
    case REG_DUTY:
      return cfg_duty;
    case REG_RES0: {
      // Reading RES0 resets the WDT, latches RES1, and (cut mode) consumes the
      // window counts. The returned value is precomputed by recompute_res(), so
      // this stays a few cycles. RES0.fault mirrors only the permanent fault
      // (cannot run); a recoverable WDT timeout surfaces via FAULT.wdt instead.
      cfg_wdt_ref = TCA0.SINGLE.CNT;
      res1_latch = res1_shadow;
      uint8_t r = res0_shadow | (fault ? 0x80 : 0x00);
      if (cfg_mode != MODE_PROBE) {
        stat_open = stat_short = stat_good = 0;  // probe result is not cleared by reading
      }
      return r;
    }
    case REG_RES1:
      return res1_latch;
    case REG_FAULT:
      return (cfg_wdt ? 0x02 : 0x00) | (fault ? 0x01 : 0x00);
  }
  return 0;
}

// TWI slave: register-pointer protocol. Each write segment starts with the
// register pointer; subsequent writes auto-increment. Reads return successive
// registers from the current pointer, auto-incrementing (so the host can read
// RES0,RES1 in one sequential read, including via a write,Sr,read transfer).
ISR(TWI0_TWIS_vect) {
  uint8_t s = TWI0.SSTATUS;

  if (s & (TWI_BUSERR_bm | TWI_COLL_bm)) {
    // Bus error / collision: drop the transaction. Per-segment state is
    // re-armed at the next address match.
    TWI0.SSTATUS = TWI_BUSERR_bm | TWI_COLL_bm;
    TWI0.SCTRLB = TWI_SCMD_COMPTRANS_gc;
    return;
  }

  if (s & TWI_APIF_bm) {
    if (s & TWI_AP_bm) {
      // Address match: ACK and proceed. A write segment always starts with a
      // pointer byte; a read segment starts from the current pointer, so the
      // pointer survives a write,Sr,read transfer.
      if (!(s & TWI_DIR_bm)) {
        i2c_ptr_written = false;
      }
      i2c_tx_first = true;
      TWI0.SCTRLB = TWI_ACKACT_ACK_gc | TWI_SCMD_RESPONSE_gc;
    } else {
      // Stop condition.
      TWI0.SCTRLB = TWI_SCMD_COMPTRANS_gc;
    }
    return;
  }

  if (s & TWI_DIF_bm) {
    if (s & TWI_DIR_bm) {
      // Master read: we transmit. After the first byte, RXACK reflects the
      // master's response to the previous byte; NACK means it wants no more.
      // On the first byte RXACK is stale (typically the NACK that ended the
      // previous read), so it must be ignored.
      if (!i2c_tx_first && (s & TWI_RXACK_bm)) {
        TWI0.SCTRLB = TWI_SCMD_COMPTRANS_gc;
      } else {
        i2c_tx_first = false;
        TWI0.SDATA = read_reg(i2c_reg_ptr++);
        TWI0.SCTRLB = TWI_SCMD_RESPONSE_gc;
      }
    } else {
      // Master write: we receive.
      uint8_t d = TWI0.SDATA;
      if (!i2c_ptr_written) {
        i2c_reg_ptr = d;
        i2c_ptr_written = true;
      } else {
        write_reg(i2c_reg_ptr++, d);
      }
      TWI0.SCTRLB = TWI_ACKACT_ACK_gc | TWI_SCMD_RESPONSE_gc;
    }
    return;
  }
}

////////////////////////////////////////////////////////////////////////////////
// Init.

static void clock_init() {
  // Run at full 20 MHz: disable prescaler (default is /6).
  CCP = CCP_IOREG_gc;
  CLKCTRL.MCLKCTRLB = 0;
}

static void pins_init() {
  // Outputs low; HV_FAULT input with pull-up (active-low). HC_CURR must be an
  // output for TCD0's waveform override to reach the pin (see hc_curr_init).
  // I2C pins are driven by TWI0 when enabled (board provides external pull-ups).
  VPORTA.OUT &= ~(HV_EN_bm | HC_EN_bm | HC_CURR_bm);
  VPORTA.DIR |= HV_EN_bm | HC_EN_bm | HC_CURR_bm;
  VPORTA.DIR &= ~(HV_CURR_bm | HV_FAULT_bm);
  PORTA.PIN3CTRL = PORT_PULLUPEN_bm;  // HV_FAULT (PA3)

  // Indicator LEDs off until boot completes.
  VPORTC.OUT &= ~(LED_OK_bm | LED_RUN_bm | LED_ERR_bm);
  VPORTC.DIR |= LED_OK_bm | LED_RUN_bm | LED_ERR_bm;
}

static void timers_init() {
  // TCB0: free-running 16-bit at CLK_PER (50 ns/tick) for intra-window timing.
  TCB0.CCMP = 0xFFFF;
  TCB0.CTRLB = TCB_CNTMODE_INT_gc;
  TCB0.CTRLA = TCB_CLKSEL_CLKDIV1_gc | TCB_ENABLE_bm;

  // TCA0: free-running 16-bit at CLK_PER/1024 (51.2 us/tick); software WDT clock.
  TCA0.SINGLE.CTRLA = TCA_SINGLE_CLKSEL_DIV1024_gc | TCA_SINGLE_ENABLE_bm;
}

// TCD0: constant-duty PWM on HC_CURR (PA5 = WOB), the HC board's current
// setting. Runs from boot and is never changed, so the HC board's 10 ms setting
// delay is always long expired by the time HC_EN goes active.
static void hc_curr_init() {
  // One ramp mode: the counter runs 0..CMPBCLR, WOB is high over the last
  // (CMPBCLR - CMPBSET) ticks. CMPA is unused but must stay ordered ahead of
  // CMPBSET.
  TCD0.CMPASET = 0;
  TCD0.CMPACLR = 1;
  TCD0.CMPBSET = HC_CURR_PERIOD_TICKS - 1 - HC_CURR_HIGH_TICKS;
  TCD0.CMPBCLR = HC_CURR_PERIOD_TICKS - 1;
  TCD0.CTRLB = TCD_WGMODE_ONERAMP_gc;
  // Override the pin with WOB only; CMPAEN stays clear so WOA leaves PA4
  // (HC_EN) as plain GPIO.
  _PROTECTED_WRITE(TCD0.FAULTCTRL, TCD_CMPBEN_bm);

  while (!(TCD0.STATUS & TCD_ENRDY_bm)) {
  }
  TCD0.CTRLA = TCD_CLKSEL_20MHZ_gc | TCD_SYNCPRES_DIV1_gc | TCD_CNTPRES_DIV1_gc | TCD_ENABLE_bm;
}

static void twi_init() {
  TWI0.SADDR = I2C_DEV_ADDR << 1;
  TWI0.SCTRLA = TWI_DIEN_bm | TWI_APIEN_bm | TWI_PIEN_bm | TWI_ENABLE_bm;
}

////////////////////////////////////////////////////////////////////////////////
// Pulse loop (foreground).

typedef enum { WIN_OPEN, WIN_SHORT, WIN_GOOD } window_type_t;

static inline bool hv_curr() {
  return VPORTA.IN & HV_CURR_bm;
}
static inline void hv_en(bool on) {
  if (on) {
    VPORTA.OUT |= HV_EN_bm;
  } else {
    VPORTA.OUT &= ~HV_EN_bm;
  }
}
static inline void hc_en(bool on) {
  if (on) {
    VPORTA.OUT |= HC_EN_bm;
  } else {
    VPORTA.OUT &= ~HC_EN_bm;
  }
}
static inline void led_set(uint8_t led_bm, bool on) {
  if (on) {
    VPORTC.OUT |= led_bm;
  } else {
    VPORTC.OUT &= ~led_bm;
  }
}

// Busy-wait via the free-running TCB0. Safe with interrupts on or off and for
// long waits: each chunk's tick count stays within uint16 (2000 us * 20 < 2^16).
static void wait_us(uint32_t us) {
  while (us > 0) {
    uint16_t chunk = us > 2000u ? 2000u : (uint16_t)us;
    uint16_t start = TCB0.CNT;
    uint16_t target = chunk * TICKS_PER_US;
    while ((uint16_t)(TCB0.CNT - start) < target) {
    }
    us -= chunk;
  }
}

// One cut-mode window. HV.EN==L && HC.EN==L on entry and exit. `use_hc` selects
// the good-pulse path: 10 A hands HV over to HC; 1 A pulses HV alone.
//
// Runs with interrupts enabled. Pulse width stays exact because the busy-waits
// are referenced to the free-running TCB0; a coincident TWI ISR perturbs an edge
// by at most its own (~2 us) duration.
static window_type_t cut_window(uint32_t pulse_dur_us, uint8_t duty_byte, bool use_hc) {
  hv_en(true);

  // Wait ignition.
  uint16_t t0 = TCB0.CNT;
  window_type_t wt;
  while (true) {
    uint16_t dt = (uint16_t)(TCB0.CNT - t0);
    bool cond = hv_curr();
    if (dt <= T_TRAN_TICKS) {
      // ignore transient period data
    } else if (dt <= T_IG_MAX_TICKS) {
      if (cond) {
        wt = dt <= T_IG_SHORT_TICKS ? WIN_SHORT : WIN_GOOD;
        break;
      }
    } else {
      wt = WIN_OPEN;
      break;
    }
  }

  if (wt == WIN_OPEN) {
    hv_en(false);
    wait_us(CD_OPEN_US);
    return WIN_OPEN;
  } else if (wt == WIN_SHORT) {
    hv_en(false);
    wait_us(CD_SHORT_US);
    return WIN_SHORT;
  }

  // Good pulse.
  if (use_hc) {
    // 10 A: keep HV.EN for PULSE_HANDOVER_US while HC warms up, then hand over
    // to HC for the rest of the pulse. Actual HV pulse shape is set by HV
    // firmware.
    hc_en(true);
    wait_us(PULSE_HANDOVER_US);
    hv_en(false);
    wait_us(pulse_dur_us - PULSE_HANDOVER_US);
    hc_en(false);
  } else {
    // 1 A: HV-only pulse; HC stays off. The HV firmware fixes the pulse width
    // (~10 us), so we just hold HV.EN for the configured duration.
    wait_us(pulse_dur_us);
    hv_en(false);
  }

  // cool_duty enforces the max-duty config. max_duty = (duty_byte + 1)/256, so
  // cool = pulse * (256/(duty+1) - 1) = pulse * (255 - duty) / (duty + 1).
  uint32_t cool_duty = pulse_dur_us * (uint32_t)(255 - duty_byte) / (duty_byte + 1);
  wait_us(cool_duty > CD_GOOD_US ? cool_duty : CD_GOOD_US);
  return WIN_GOOD;
}

// Returns true if conducted. HV.EN is OFF afterwards in all cases.
// Probe cycle: 500us (100us check phase + 400us wait, to reduce electrolysis).
// Runs with interrupts enabled (see cut_window).
static bool probe_window() {
  uint16_t t0 = TCB0.CNT;
  hv_en(true);

  bool result = false;
  while (true) {
    uint16_t dt = (uint16_t)(TCB0.CNT - t0);
    bool cond = hv_curr();

    if (dt <= T_TRAN_TICKS) {
      // ignore transient response
    } else if (dt <= PROBE_CHECK_TICKS) {
      // latch to true. Immediately turn off to minimize electrode damage.
      if (cond) {
        result = true;
        hv_en(false);
      }
    } else if (dt < PROBE_CYCLE_TICKS) {
      hv_en(false);
    } else {
      break;
    }
  }
  return result;
}

// Permanent fault: outputs safe, sticky flag set, run cleared. Interrupts stay
// enabled so the host can still read the FAULT register.
static void enter_fault() {
  hv_en(false);
  hc_en(false);
  fault = true;
  cfg_run = false;
}
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
int main() {
  clock_init();
  pins_init();
  timers_init();
  hc_curr_init();

  // Seed registers to reset defaults, keeping the DUR/DUTY invariant in range.
  cfg_mode = MODE_ON_RESET;
  cfg_curr = clamp_curr(CURR_ON_RESET);
  cfg_dur = DUR_ON_RESET;
  cfg_duty = DUTY_ON_RESET;
  reclamp_dur();
  recompute_res();  // seed the shadow before the TWI ISR can serve a RES0 read

  twi_init();
  sei();

  // Boot self-test: HV_CURR is expected L. H means a hardware fault; latch the
  // permanent fault.
  wait_us(250 * 1000L);  // wait for all power to settle
  if (hv_curr()) {
    enter_fault();
  } else {
    led_set(LED_OK_bm, true);  // successful boot
  }

  while (true) {
    // Refresh the RES0/RES1 shadow from the previous iteration's stats, so the
    // ISR's RES0 read stays cheap. Covers cut/probe/idle and the post-run-start
    // reset uniformly.
    recompute_res();

    // Atomic snapshot of config + WDT reference (multi-byte values shared with
    // the ISR). Also sample the hardware fault input.
    bool run, fault_now;
    uint8_t mode, curr, dur_byte, duty_byte;
    uint16_t wdt_ref;
    ATOMIC_BLOCK(ATOMIC_RESTORESTATE) {
      run = cfg_run;
      mode = cfg_mode;
      curr = cfg_curr;
      dur_byte = cfg_dur;
      duty_byte = cfg_duty;
      wdt_ref = cfg_wdt_ref;
    }
    fault_now = fault || !(VPORTA.IN & HV_FAULT_bm);  // HV_FAULT is active-low

    // Indicators lag state changes by at most one loop iteration (~100 us).
    led_set(LED_RUN_bm, run && !fault_now);
    led_set(LED_ERR_bm, fault_now || cfg_wdt);

    if (fault_now) {
      enter_fault();
      wait_us(100);  // idle; interrupts on, ISR serves FAULT reads
      continue;
    }

    if (!run) {
      wait_us(100);
      continue;
    }

    // WDT: host must read RES0 within WDT_TIMEOUT_US. Timeout latches wdt and
    // stops the device (recoverable).
    if ((uint16_t)(TCA0.SINGLE.CNT - wdt_ref) >= WDT_TIMEOUT_TICKS) {
      ATOMIC_BLOCK(ATOMIC_RESTORESTATE) {
        cfg_wdt = true;
        cfg_run = false;
      }
      continue;
    }

    if (mode == MODE_PROBE) {
      if (probe_window()) {
        ATOMIC_BLOCK(ATOMIC_RESTORESTATE) {
          cfg_probe_detected = true;
          cfg_run = false;  // probe stops on detection
        }
      }
    } else {
      uint32_t pulse_dur_us = dur_decode_us(dur_byte);
      window_type_t w = cut_window(pulse_dur_us, duty_byte, curr == CURR_10A);
      ATOMIC_BLOCK(ATOMIC_RESTORESTATE) {
        switch (w) {
          case WIN_OPEN:
            stat_open++;
            break;
          case WIN_SHORT:
            stat_short++;
            break;
          case WIN_GOOD:
            stat_good++;
            break;
        }
      }
    }
  }
}

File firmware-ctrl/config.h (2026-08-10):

// SPDX-License-Identifier: BSD-2-Clause
#pragma once

#include <stdint.h>

/**
 * ATtiny1616 controller firmware for the PULSER ctrl board.
 *
 * Device spec: docs/i2c-registers.md (I2C register map) and docs/operation.md
 * (window/timing model). The pulse loop runs in the foreground and the I2C
 * slave runs in the TWI ISR (see main.c).
 */

/**
 * I2C host interface.
 */
#define I2C_DEV_ADDR 0x3c

/**
 * GPIO pin assignments (ctrl board).
 *
 * HV/HC signals are all on PORTA, indicator LEDs on PORTC. I2C uses the TWI0
 * default pins PB0=SCL, PB1=SDA (routed automatically when TWI0 is enabled;
 * no PORTMUX needed).
 */
#define HV_EN_bm    PIN1_bm  // PA1, output: HV gate enable, active H
#define HV_CURR_bm  PIN2_bm  // PA2, input:  comparator out, idle L, H = current detected
#define HV_FAULT_bm PIN3_bm  // PA3, input:  HV board fault, active L; latches permanent fault
#define HC_EN_bm    PIN4_bm  // PA4, output: HC gate enable, active H
#define HC_CURR_bm  PIN5_bm  // PA5, output: HC current setting, PWM driven by TCD0 WOB

// Indicator LEDs, all active H (pin -> LED -> resistor -> GND).
#define LED_OK_bm  PIN0_bm  // PC0, green: successful boot
#define LED_RUN_bm PIN1_bm  // PC1, amber: output enabled
#define LED_ERR_bm PIN2_bm  // PC2, red:   fault (permanent or latched WDT timeout)

/**
 * HC current setting (HC.CURR). See docs/hc.md: PWM in the 10 kHz - 200 kHz
 * band, duty selects the output current, 45% = 10 A (above that the HC board
 * clamps internally). HC only ever carries the 10 A case (CURR = 1 A is
 * HV-only), so the duty is a constant.
 *
 * Driven by TCD0 WOB, which clocks off the 20 MHz oscillator directly rather
 * than CLK_PER; period ticks are therefore counted at 20 MHz independently of
 * F_CPU.
 */
#define HC_CURR_PWM_HZ       100000UL                       // mid-band, 0.5%/tick duty resolution
#define HC_CURR_PWM_DUTY_PCT 45                             // 10 A
#define HC_CURR_PERIOD_TICKS (20000000UL / HC_CURR_PWM_HZ)  // 200
#define HC_CURR_HIGH_TICKS   (HC_CURR_PERIOD_TICKS * HC_CURR_PWM_DUTY_PCT / 100)  // 90

/**
 * Window timing. See docs/operation.md.
 */
#define T_TRAN_US         3    // ignore period of AC transient current (capacitive coupling)
#define T_IG_SHORT_US     7    // ignition delay <= this -> short window
#define T_IG_MAX_US       500  // no ignition within this -> open window
#define CD_GOOD_US        15   // min cooldown after good window (de-arc)
#define CD_SHORT_US       100  // cooldown after short window; must exceed HV internal cooldown
#define CD_OPEN_US        500  // cooldown after open window
#define PULSE_HANDOVER_US 5    // HV+HC overlap during handover

/**
 * Watchdog: while running, host must read RES0 within this window. Timeout
 * is treated as a recoverable fault and stops the device.
 */
#define WDT_TIMEOUT_US 50000  // 50 ms

/**
 * Derived timer-tick constants.
 *
 * Fine timer TCB0 runs at CLK_PER = 20 MHz => 50 ns/tick, so ticks = us * 20.
 * The ignition-detect loop compares against these precomputed thresholds to
 * stay free of multiply/divide. A single window never exceeds the 16-bit range
 * (~3.3 ms), so elapsed time is a wrap-safe uint16 subtraction.
 */
#define TICKS_PER_US      (F_CPU / 1000000UL)
#define T_TRAN_TICKS      (T_TRAN_US * TICKS_PER_US)      // 60
#define T_IG_SHORT_TICKS  (T_IG_SHORT_US * TICKS_PER_US)  // 140
#define T_IG_MAX_TICKS    (T_IG_MAX_US * TICKS_PER_US)    // 10000
#define PROBE_CHECK_TICKS (100u * TICKS_PER_US)           // 2000  (probe latch phase)
#define PROBE_CYCLE_TICKS (500u * TICKS_PER_US)           // 10000 (probe total cycle)

/**
 * Coarse timer TCA0 runs at CLK_PER / 1024 = 51.2 us/tick, used as the software
 * WDT clock. 50 ms / 51.2 us = 976.6 -> 977 ticks. uint16 wrap-safe (period is
 * ~3.35 s, far longer than the 50 ms timeout).
 */
#define WDT_TIMEOUT_TICKS 977u

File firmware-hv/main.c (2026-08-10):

// SPDX-License-Identifier: AGPL-3.0-or-later
#define F_CPU 20000000UL

#include <avr/io.h>
#include <stdbool.h>
#include <util/delay.h>

/* -- Pin definitions ------------------------------------------------ */

#define LED_STAT_bm  PIN3_bm  // PC3
#define LED_FAULT_bm PIN2_bm  // PC2
#define GATE_bm      PIN4_bm  // PA4
#define EN_bm        PIN0_bm  // PC0
#define CURR_bm      PIN1_bm  // PC1
#define N_FAULT_bm   PIN0_bm  // PB0
// VTH: PA6, DAC0 output (comparator current threshold); configured in dac_init()

/* -- Pulse configuration -------------------------------------------- */

#define PULSE_DUR_US    10
#define COOLDOWN_DUR_US 100
#define THRESH_MA       500

/* -- Pin initialization --------------------------------------------- */

static void pins_init() {
  // STAT LED PC3: output, initially off
  VPORTC.DIR |= LED_STAT_bm;
  VPORTC.OUT &= ~LED_STAT_bm;

  // N_FAULT PB0 & FAULT LED PC2: outputs, initially de-asserted
  VPORTB.OUT |= N_FAULT_bm;
  VPORTB.DIR |= N_FAULT_bm;
  VPORTC.OUT &= ~LED_FAULT_bm;
  VPORTC.DIR |= LED_FAULT_bm;

  // GATE PA4: output, initially low
  VPORTA.DIR |= GATE_bm;
  VPORTA.OUT &= ~GATE_bm;

  // EN PC0: input, internal pull-up (not ideal, but better than high-Z)
  VPORTC.DIR &= ~EN_bm;
  PORTC.PIN0CTRL = PORT_PULLUPEN_bm;

  // CURR PC1: input, no pull (driven by external comparator)
  VPORTC.DIR &= ~CURR_bm;
}

/* -- STAT LED ------------------------------------------------------- */

static void stat_led(bool on) {
  if (on) {
    VPORTC.OUT |= LED_STAT_bm;
  } else {
    VPORTC.OUT &= ~LED_STAT_bm;
  }
}

/* -- Fault mode ---------------------------------------------------- */

static void fault_mode() __attribute__((noreturn));
static void fault_mode() {
  VPORTA.OUT &= ~GATE_bm;
  VPORTB.OUT &= ~N_FAULT_bm;
  VPORTC.OUT |= LED_FAULT_bm;
  while (1) {
  }
}

/* -- Elapsed-time timer (pulse & duty timing) ---------------------- */

// Free-running 16-bit counter at CLK_PER (20 MHz) -> 20 ticks/µs.
#define TICKS_PER_US (F_CPU / 1000000UL)

static void timer_init() {
  TCB0.CCMP = 0xFFFF;
  TCB0.CTRLB = TCB_CNTMODE_INT_gc;
  TCB0.CTRLA = TCB_CLKSEL_CLKDIV1_gc | TCB_ENABLE_bm;
}

static void timer_reset() {
  TCB0.CNT = 0;
}

// Warning: wraps 3276 µs after timer_reset().
static uint16_t timer_elapsed_ticks() {
  return TCB0.CNT;
}

/* -- DAC initialization (VTH output) ------------------------------- */

static void dac_init() {
  VREF.CTRLA = VREF_DAC0REFSEL_4V34_gc;
  DAC0.DATA = (uint16_t)THRESH_MA * 128 / 434;
  DAC0.CTRLA = DAC_ENABLE_bm | DAC_OUTEN_bm;
}

/* -- Main ----------------------------------------------------------- */

int main() {
  // Run at full 20 MHz: disable prescaler (default is /6)
  CCP = CCP_IOREG_gc;
  CLKCTRL.MCLKCTRLB = 0;

  pins_init();
  dac_init();
  timer_init();
  _delay_ms(10);  // wait DAC & comparator stabilization
  stat_led(true);

  // Current shouldn't be flowing; H indicates some kind of hardware fault.
  if (VPORTC.IN & CURR_bm) {
    fault_mode();
  }

  const uint16_t pulse_ticks = PULSE_DUR_US * TICKS_PER_US;
  const uint16_t cooldown_ticks = COOLDOWN_DUR_US * TICKS_PER_US;

  while (1) {
    // Pre-pulse safety: CURR high without GATE means hardware fault
    //if (VPORTC.IN & CURR_bm) {
//      fault_mode();
    //}

    // Wait for EN rise & activate output
    while (!(VPORTC.IN & EN_bm)) {
    }
    VPORTA.OUT |= GATE_bm;

    // Wait for current to appear, abort if EN drops
    while (!(VPORTC.IN & CURR_bm)) {
      if (!(VPORTC.IN & EN_bm)) {
        VPORTA.OUT &= ~GATE_bm;
        goto wait_en_low;
      }
    }
    timer_reset();  // CURR rise is the reference for both durations

    // Current flowing: hold gate until the pulse elapses or EN drops
    while (timer_elapsed_ticks() < pulse_ticks) {
      if (!(VPORTC.IN & EN_bm)) {
        break;
      }
    }
    VPORTA.OUT &= ~GATE_bm;

    // Thermal duty limit: output stays off for the rest of the window
    while (timer_elapsed_ticks() < cooldown_ticks) {
    }

  wait_en_low:
    while (VPORTC.IN & EN_bm) {
    }
  }
}

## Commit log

2024-08-11 Init (STL 2D slicing)
2024-12-12 Draft of PCB layout
2024-12-19 Add assembly proc for ED
2025-01-23 Restructure repo dirs
    [AD-MSOP-LT8365.step, Bourns_Fuse_SF_6.1x2.6.step, CTRL-MINI-ED-sim-dchg.kicad_sch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]
2025-01-23 Specify ED board (board + FW)
2025-01-23 Add ED PCB cheatsheet for uC. Update I2C to use int reg.
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2025-01-24 Bug fixes and code refactor
    [config.h, main.c]
2025-01-24 Remove no longer relevant ED commands from CTRL-MINI
    [main.c]
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2025-01-28 Wait until ED board is up
2025-01-28 Add missing critical section init
    [main.c]
2025-01-28 Update ED test instruction & LED error blink
    [main.c]
2025-01-28 Unify to mA to avoid confusion
    [main.c]
2025-01-28 Rename pcb & firmware to be more meaningful
    [CORE.kicad_pcb, CORE.kicad_sch, CTRL-MINI-ED-sim-sense.kicad_sch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]
2025-02-09 Apply strict warning and fix thresh pwm bug
    [main.c]
2025-02-09 Fix potential thresh-curr mismatch path
    [main.c]
2025-02-10 Enlarge short detection thresh
    [main.c]
2025-02-10 1us window GATE noise filtering
    [main.c]
2025-02-13 Add bode plot analysis of opamp-mosfet-load-rsense loop
    [PULSER-sim-control.kicad_sch]
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2025-02-24 PULSER r2 pulse shaper draft
    [PULSER-sim-dchg.kicad_sch, PULSER.kicad_pcb, PULSER.kicad_sch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]
2025-02-25 PULSER r2 schematics ok
    [Omron_Relay_DPDT2C_G2R.step, PULSER-sim-control.kicad_sch, PULSER.kicad_pcb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]
2025-02-26 PULSER r2 PCB draft
    [PG-TDSON-8.step, PULSER.kicad_pcb, PULSER.kicad_sch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]
2025-02-26 Setup 3D files
    [PQ2614B.step, PULSER.kicad_pcb]
2025-02-26 Power block done
    [PULSER.kicad_pcb, mux_half_bridge.kicad_sch, pulse_shaper.kicad_sch]
2025-02-27 Fix caps, improve schematic docs
    [PULSER.kicad_sch, boost_converter_100v.kicad_sch, mux_half_bridge.kicad_sch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]
2025-02-27 before mass vias
    [PULSER.kicad_pcb, boost_converter_100v.kicad_sch, pico2.kicad_sch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]
2025-02-27 Stich GND by vias
    [PULSER.kicad_pcb]
2025-02-27 Improve GND handling
    [PULSER.kicad_pcb]
2025-02-27 Pulser r2 gerber
    [PULSER.kicad_pcb, bom.csv, designators.csv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]
2025-02-27 Update parts soucing
    [PULSER.kicad_pcb, PULSER.kicad_sch, boost_converter_100v.kicad_sch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]
2025-02-27 Alt sources
    [boost_converter_100v.kicad_sch, pulse_shaper.kicad_sch]
2025-02-28 Fix FCC conn orientation, fix diode DFM issues
    [PULSER.kicad_pcb, bom.csv, positions.csv]
2025-03-01 Update motor for belt drive
2025-03-01 Remove hard-code from drill speed feedback
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2025-03-06 Fix I2C type error
2025-03-06 Fix eps related error
    [config.h, main.c]
2025-03-06 Avoid unncessary double FP
    [main.c]
2025-03-06 Improve pulser i/f. Fix find error after 1st time
    [config.h, main.c]
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2025-03-07 Stabilize new feedback control
    [config.h, main.c]
2025-03-09 Find issue was due to hardware failure. Revert current change
    [main.c]
2025-03-18 Fix temp sensor I2C & current offset
    [main.c]
2025-03-20 Implement short detection disable for testing
    [main.c]
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2025-03-21 Fix current conversion
2025-03-26 Reduce gain to lower overshoot
    [main.c]
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2025-03-27 PULSER r3 schematics draft
    [PULSER.kicad_pcb, PULSER.kicad_sch, boost_converter_100v.kicad_sch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]
2025-03-27 PULSER r3 PCB DRC pass
    [PULSER.kicad_pcb, PULSER.kicad_sch, boost_converter_100v.kicad_sch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]
2025-03-27 PULSER r3 JLCPCB files
    [PULSER.kicad_pcb, bom.csv, designators.csv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]
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2025-04-08 Fix denoiser for GATE
    [main.c]
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2025-06-08 Make it pulser-only
    [CORE.kicad_pcb, CORE.kicad_sch, STPDRV.kicad_pcb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]
2025-07-30 Fix missing 5V input
    [PULSER.kicad_pcb, PULSER.kicad_sch, boost_converter_100v.kicad_sch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]
2025-08-05 EMI reduction & heatsink simplification
    EMI: MOSFET snubber, 36V pi-filter
    heatsink: Parallel mux bridge
    [PULSER.kicad_sch, boost_converter_100v.kicad_sch, mux_half_bridge.kicad_sch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]
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2025-08-05 EMI (ferrite for I2C). Simplify I2C signal
    [PULSER.kicad_sch, boost_converter_100v.kicad_sch, mux_half_bridge.kicad_sch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]
2025-08-05 r4 DRC pass
    [PULSER.kicad_pcb]
2025-08-05 Bump revision to r4
    [PULSER.kicad_pcb, PULSER.kicad_sch, boost_converter_100v.kicad_sch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]
2025-08-05 Export r4
    [bom.csv, designators.csv, positions.csv]
2025-08-06 Increase current path width
    [PULSER.kicad_pcb]
2025-08-06 Fix mux MOSFET LCSC ids
    [PULSER.kicad_sch, boost_converter_100v.kicad_sch, mux_half_bridge.kicad_sch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]
2025-08-12 Replace gate input w/ ckp timeout
    [config.h, main.c]
2025-11-12 (crit) Insert resistor to 100V line / (minor) Fix small diode foorprint
    [PULSER.kicad_pcb, PULSER.kicad_sch, boost_converter_100v.kicad_sch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]
2025-11-12 export PCBA data
    [bom.csv, designators.csv, positions.csv]
2025-11-12 Add alternative LCSC no
    [pulse_shaper.kicad_sch]
2025-11-23 Lower ignition detection threshold current to avoid burning 100V circuit
    [main.c]
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2025-12-03 Fix timing accuracy of ignite()
    [main.c]
2026-01-07 pcb lib: add LT3741-1 & fix part bg colors
2026-01-07 Upgrade KiCad & new discharge exps
    [PULSER-sim-dchg.kicad_sch]
2026-01-07 Init test boards for HV, HC modules
    [PULSER-testboard-hc.kicad_pcb, PULSER-testboard-hc.kicad_sch, PULSER-testboard-hv.kicad_pcb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]
2026-01-08 Draft architecture for both HC & HV
    [PULSER-testboard-hc.kicad_sch, boost.kicad_sch, pulse.kicad_sch]
2026-01-11 HC testboard: schem draft ok
    [PULSER-testboard-hc.kicad_pcb, PULSER-testboard-hc.kicad_sch]
2026-01-12 HC test board pcb draft ok
    [PULSER-testboard-hc.kicad_pcb, PULSER-testboard-hc.kicad_sch]
2026-01-13 HV schem draft ok
    [PULSER-testboard-hv.kicad_pcb, PULSER-testboard-hv.kicad_sch, boost.kicad_sch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]
2026-01-13 HV lcsc & footprint assigned
    [PULSER-testboard-hv.kicad_pcb, PULSER-testboard-hv.kicad_sch, boost.kicad_sch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]
2026-01-13 HC, HV: PCB DRC pass
    [PULSER-testboard-hc.kicad_pcb, PULSER-testboard-hc.kicad_sch, PULSER-testboard-hv.kicad_pcb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]
2026-01-14 Add I/O descs
    [PULSER-testboard-hc.kicad_pcb, PULSER-testboard-hv.kicad_pcb]
2026-01-14 pcb: replace abs path w/ relative path
    [PULSER-testboard-hc.kicad_pcb, PULSER-testboard-hv.kicad_pcb, PULSER.kicad_pcb]
2026-01-14 HV, HC: export for jlcpcb
    [bom.csv, designators.csv, positions.csv]
2026-01-14 HC: add missing LCSC number
    [PULSER-testboard-hc.kicad_pcb, PULSER-testboard-hc.kicad_sch, bom.csv]
2026-01-14 HV: Fix wrong LCSC number
    [PULSER-testboard-hv.kicad_pcb, PULSER-testboard-hv.kicad_sch, bom.csv]
2026-02-04 HC TestBoards r2 schem draft ok
    [PULSER-testboard-hc.kicad_sch]
2026-02-05 HC TestBoard r2 PCB draft ok
    [PULSER-testboard-hc.kicad_pcb, PULSER-testboard-hc.kicad_sch]
2026-02-06 JLCPCB ready
    [bom.csv, designators.csv, positions.csv]
2026-02-06 HV TestBoard r2 schem draft ok. mock firmware build env.
    [PULSER-testboard-hv.kicad_sch, boost.kicad_sch, pulse.kicad_sch]
2026-02-06 HV TestBoard r2 pcb ok
    [PULSER-testboard-hv.kicad_pcb, PULSER-testboard-hv.kicad_sch, bom.csv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]
2026-04-15 P2HV r3 schem
    [PULSER-testboard-hv.kicad_sch, boost.kicad_sch, pulse.kicad_sch]
2026-04-15 P2HV r3 PCB
    [PULSER-testboard-hv.kicad_pcb, PULSER-testboard-hv.kicad_sch, bom.csv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]
2026-05-06 Prevent mis-classification of short pulse as normal pulse
    [main.c]
2026-05-22 Got rid of unstable V1
    [PULSER-sim-dchg.kicad_sch, PULSER.kicad_pcb, PULSER.kicad_sch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]
2026-05-22 Record test controller (breardboard) schematics
    [PULSER-testboard-ctrl.kicad_pcb, PULSER-testboard-ctrl.kicad_sch]
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2026-05-22 Record current testboard modifications as schematics
    [PULSER-testboard-hc.kicad_sch, PULSER-testboard-hv.kicad_sch]
2026-05-28 Spec out new I2C register map w/ probe function
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2026-06-04 Distinguish tran noise vs short
    [config.h, main.c]
2026-06-25 Cooling design test
    [duct.FCStd, mock-fan.FCStd, mock-heatsink.FCStd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]
2026-06-25 Back-fan design
    [duct.FCStd, pcb-assy.FCStd]
2026-06-29 Bigger duct & HS
    [duct.FCStd, mock-fan.FCStd, mock-heatsink.FCStd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]
2026-06-30 Add module foot
    [duct.FCStd, pcb-assy.FCStd]
2026-06-30 Add TPSM365 to lib
    [TI-RDN0011A.stp]
2026-06-30 Draft ctrl r2 schem
    [PULSER-testboard-ctrl.kicad_sch]
